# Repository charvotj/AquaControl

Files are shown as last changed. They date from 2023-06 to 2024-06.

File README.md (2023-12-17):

# Do not read me :)

It's work in progress and it's still completely uncomplete.

## Pro průběžný progress:
- [Verze odevzdaná jako semestrální](https://github.com/charvotj/AquaControl/tree/main/Semestr%C3%A1lka%20k%20odevzd%C3%A1n%C3%AD)
- [Poslední LaTeX build (text práce)](https://github.com/charvotj/AquaControl/blob/main/latex/CharvotBakalarka2023.pdf)
- [Schéma řídící jednotky (export do pdf)](https://github.com/charvotj/AquaControl/blob/main/latex/obrazky/exportovane/main-board-schematic.pdf)

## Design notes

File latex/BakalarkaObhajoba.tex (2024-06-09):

% Soubory musí být v kódování, které je nastaveno v příkazu \usepackage[...]{inputenc}

\documentclass[%        Základní nastavení
  %draft,    				  % Testovací překlad
  12pt,       				% Velikost základního písma je 12 bodů
	t,                  % obsah slajdů bude vždy začínat od shora (nebude vertikálně centrovaný)
	aspectratio=1610,   % poměr stran bude 16:10 (všechny projektory v učebnách na Technické 12 Brno),
	                    % další volby jsou 43, 149, 169, 54, 32.
	unicode,						% Záložky a informace budou v kódování unicode
]{beamer}				    	% Dokument třídy 'zpráva', vhodná pro sazbu závěrečných prací s kapitolami
%\usepackage{etex}

\usepackage[utf8]		  % Kódování zdrojových souborů je v UTF-8
	{inputenc}					% Balíček pro nastavení kódování zdrojových souborů
	
\usepackage{graphicx} % Balíček 'graphicx' pro vkládání obrázků
											% Nutné pro vložení logotypů školy a fakulty
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

\usepackage{cmap} 		% Balíček cmap zajišťuje, že PDF vytvořené `pdflatexem' je
											% plně "prohledávatelné" a "kopírovatelné"

%\usepackage{upgreek}	% Balíček pro sazbu stojatých řeckých písmem
											%% např. stojaté pí: \uppi
											%% např. stojaté mí: \upmu (použitelné třeba v mikrometrech)
											%% pozor, grafická nekompatibilita s fonty typu Computer Modern!

%\usepackage{amsmath} %balíček pro sabu náročnější matematiky

\usepackage{booktabs} % Balíček, který umožňuje v tabulce používat
                      % příkazy \toprule, \midrule, \bottomrule

%%%%%%%%%%%%%%%%%%%%%%%%%%%%%%%%%%%%%%%%%%%%%%%%%%%%%%%%%%%%%%%%%
%%%%%%      Definice informací o dokumentu             %%%%%%%%%%
%%%%%%%%%%%%%%%%%%%%%%%%%%%%%%%%%%%%%%%%%%%%%%%%%%%%%%%%%%%%%%%%%

\input{nastaveni}      % v tomto souboru doplňte údaje o sobě, o názvu práce...
                       % (tento soubor je sdílený s textem práce)

%%%%%%%%%%%%%%%%%%%%%%%%%%%%%%%%%%%%%%%%%%%%%%%%%%%%%%%%%%%%%%%%%%%%%%%%

%%%%%%%%%%%%%%%%%%%%%%%%%%%%%%%%%%%%%%%%%%%%%%%%%%%%%%%%%%%%%%%%%%%%%%%%
%%%%%%     Nastavení polí ve Vlastnostech dokumentu PDF      %%%%%%%%%%%
%%%%%%%%%%%%%%%%%%%%%%%%%%%%%%%%%%%%%%%%%%%%%%%%%%%%%%%%%%%%%%%%%%%%%%%%
%% Při vloženém balíčku 'hyperref' lze použít příkaz '\pdfsettings'
\pdfsettings
%  Nastavení polí je možné provést také ručně příkazem:
%\hypersetup{
%  pdftitle={Název studentské práce},    	% Pole 'Document Title'
%  pdfauthor={Autor studenstké práce},   	% Pole 'Author'
%  pdfsubject={Typ práce}, 						  	% Pole 'Subject'
%  pdfkeywords={Klíčová slova}           	% Pole 'Keywords'
%}
\hypersetup{pdfpagemode=FullScreen}       % otevření rovnou v režimu celé obrazovky
%%%%%%%%%%%%%%%%%%%%%%%%%%%%%%%%%%%%%%%%%%%%%%%%%%%%%%%%%%%%%%%%%%%%%%%

\usetheme{VUT} 				% barvy a rozložení prezentace odpovídající VUT FEKT
% alternativně lze použít jiná berevná témata, ale bez záruky. Například: 
%\usetheme{Darmstadt} \usecolortheme{default2}
\logoheader					% vytvoření zkráceného loga VUT FEKT v hlavičce slajdu, nechte odkomentované

					   %%%%%%%%%%%%%%%%%%%%%%%%%%%%%%%%%%%%%%%%%%%%%%%%%%%%%%%%%%%%%%%%%
%%%%%%      !!! VLASTNÍ BALÍČKY A NASTAVENÍ !!!        %%%%%%%%%%
%%%%%%%%%%%%%%%%%%%%%%%%%%%%%%%%%%%%%%%%%%%%%%%%%%%%%%%%%%%%%%%%%
%====== Units =====
% \usepackage{siunitx}
% \sisetup{inter-unit-product =\ensuremath{\cdot}}
% \sisetup{group-digits = integer}
% \sisetup{output-decimal-marker = {,}}
% \sisetup{exponent-product = \ensuremath{\cdot}}
% \sisetup{separate-uncertainty}
% \sisetup{tight-spacing = false}
% \DeclareSIUnit\permille{\text{\textperthousand}}
%\sisetup{scientific-notation = true}
%\sisetup{round-mode=places,round-precision=4}
%\sisetup{evaluate-expression}

%====== Hyperlinky ====== 
% \hypersetup{allbordercolors={1 1 1}}

%====== Obrazky ========
% \usepackage{graphicx} 
% \usepackage[dvipsnames]{xcolor} % E: option clash for package xcolor
% \usepackage{tikz}

% ^^ už tam někde prý jsou použité

\usepackage[siunitx]{circuitikz}
% \usepackage{pgf}
% \usetikzlibrary{matrix}
\usetikzlibrary{fit}
% \usetikzlibrary{patterns}
% \usepackage{tkz-euclide}
% \usetikzlibrary{arrows.meta, bending, patterns.meta, ducks}
% \usetikzlibrary{shapes, backgrounds, decorations.pathmorphing, calc}
\usetikzlibrary{positioning}

% % \usepackage{derivative} % nebude potřeba 

% \usepackage{pgfplots}
% \pgfplotsset{width=0.8\linewidth, compat=1.17}
% \def\plotcscale{0.8}
% \usepackage{pgfplotstable}
% \newcommand*\circled[1]{\tikz[baseline=(char.base)]{
%             \node[shape=circle,draw,inner sep=1pt] (char) {#1};}}

% \usepackage[style=iso-numeric,backend=biber]{biblatex}
% \addbibresource{text/literatura.bib}
%making everything to match Juice citations
% \DeclareFieldFormat{labelnumberwidth}{\mkbibbrackets{#1}}
% \usepackage{natbib}
% \usepackage{url}
% \DeclareUrlCommand\url{\def\UrlLeft{<}\def\UrlRight{>} \urlstyle{tt}}

% TEMP
\usepackage{multirow}
\usepackage{array}
\usepackage{tabularx}
\usepackage{calc}

\begin{document}

% v případě zakomentování následujícího se zobrazí v pravém dolním rohu slajdů klikatelné navigační symboly 
\disablenavigationsymbols

% titulní snímek, vysazen bez horních, dolních a postranních lišt (volba plain),
% není tak vysazen ani nadpis snímku
\maketitle

%%%%%%%%%%%%%%%%%%%%%%%%%%%%%%%%%%%%%%%%%%%%%%%%%%%%%%%%%%%%%%%%%%%%%%%
% 1. snímek s cíli (zadaním) práce
\begin{frame} 
	% nadpis snímku
	\frametitle{Cíle práce}
	Navrhnout zařízení pro automatické monitorování a řízení akvária:\\[0ex]
	%
	\begin{itemize}
		\item Průzkum trhu
		\item Stanovení požadavků
		\item Návrh zařízení
		\item Výroba
		\item Testování
	\end{itemize}
\end{frame}

% endregion

%%%%%%%%%%%%%
\begin{frame}[fragile]
	\frametitle{Průzkum trhu -- komerční řešení}
	
	\begin{columns}[T] 								% prostředí sloupce s umístěním nahoře
		\begin{column}{0.5\textwidth}		% první sloupec
			\begin{block}{Výhody}
				\begin{itemize}
					\item Všestrannost 
					\item Spolehlivost
				\end{itemize}
			\end{block}
			%
			\vspace{1.5ex}%
			\begin{alertblock}{Nevýhody}
				\begin{itemize}
					\item Vysoká cena 
					\item Převážně velmi komplexní
					\item Náročné nastavení systému
				\end{itemize}
			\end{alertblock}
			%
		\end{column}
		%
		\begin{column}{0.5\textwidth}		% druhý sloupec
			\begin{figure}%	
				\centering
				\vspace{-0.8cm}	              % horizontální mezera
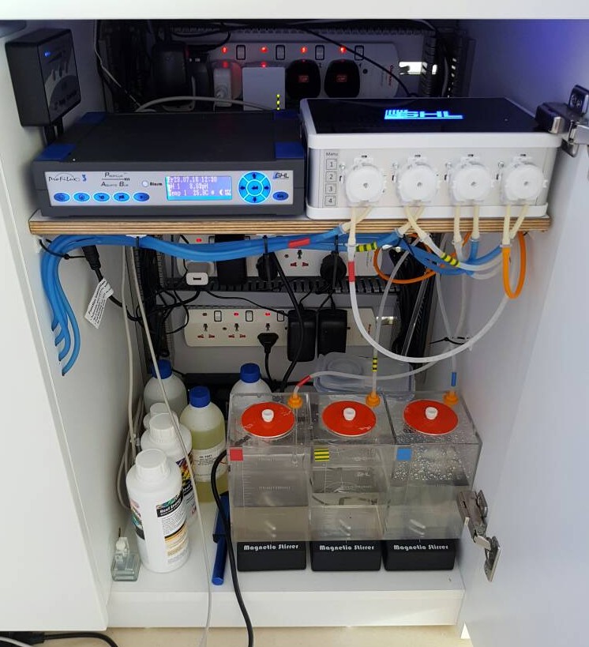
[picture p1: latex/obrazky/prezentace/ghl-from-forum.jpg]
				
				%lze vložit popisek, ale povetšinou je to v prezentaci zbytečné
				%\caption{Popisek obrázku}%
				%\label{obr:ukazka}
			\end{figure}
		\end{column}
	\end{columns}											% ukončení prostředí sloupce
\end{frame}

%%%%%%%%%%%%%
\begin{frame}[fragile]
	\frametitle{Průzkum trhu -- hobby řešení}
	
	\begin{columns}[T] 								% prostředí sloupce s umístěním nahoře
		\begin{column}{0.5\textwidth}		% první sloupec
			\begin{block}{Výhody}
				\begin{itemize}
					\item Návrh na míru 
					\item Nízká cena
				\end{itemize}
			\end{block}
			%
			\vspace{1.5ex}%
			\begin{alertblock}{Nevýhody}
				\begin{itemize}
					\item Návrh na míru
					\item Špatně rozšiřitelné
				\end{itemize}
			\end{alertblock}
			%
		\end{column}
		%
		\begin{column}{0.5\textwidth}		% druhý sloupec
			\begin{figure}%	
				\centering
				\vspace{-0.8cm}	              % horizontální mezera
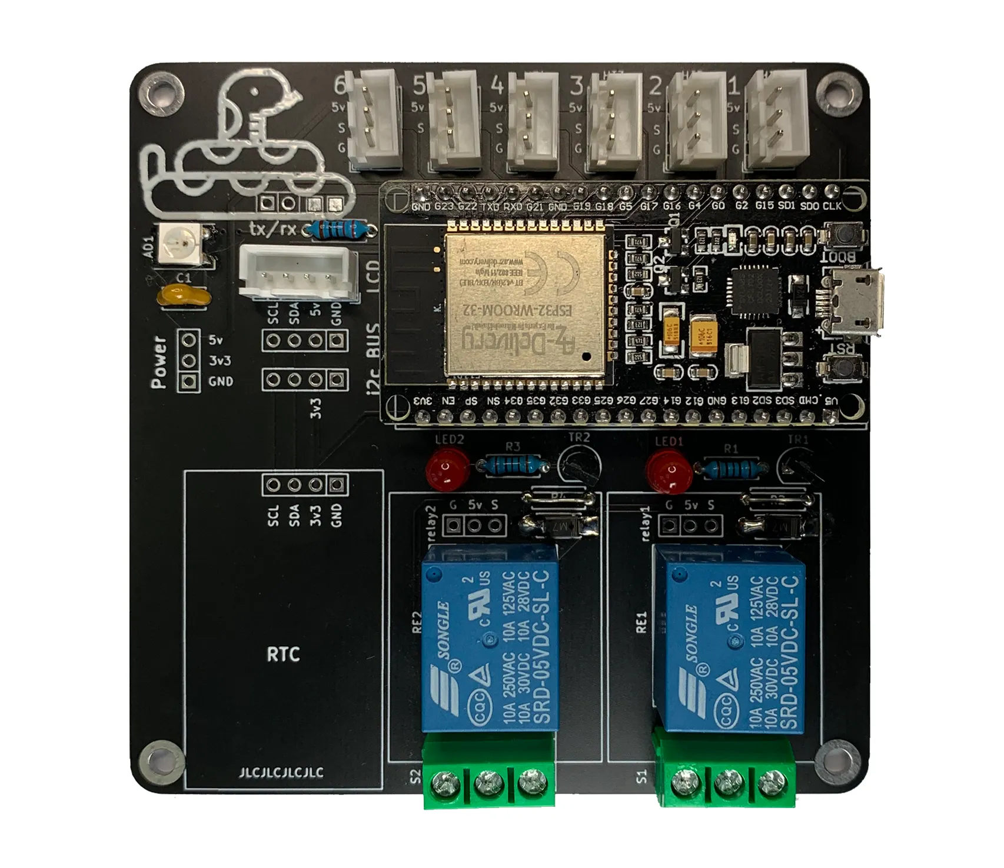
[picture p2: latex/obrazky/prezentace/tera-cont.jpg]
				
				%lze vložit popisek, ale povetšinou je to v prezentaci zbytečné
				%\caption{Popisek obrázku}%
				%\label{obr:ukazka}
			\end{figure}
		\end{column}
	\end{columns}											% ukončení prostředí sloupce
\end{frame}

%%%%%%%%%%%%%
\begin{frame}[fragile]
	\frametitle{Návrh vlastního zařízení -- Specifikace požadavků}
	
	\begin{columns}[T] 								% prostředí sloupce s umístěním nahoře
		\begin{column}{0.8\textwidth}		% první sloupec
			Určení zařízení:\\[1ex]
			%
			\begin{itemize}
				\item Malé sladkovodní akvária bez specifických potřeb
				\item Ovládání základních akčních členů a senzorů
			\end{itemize}
			\vspace{1.5ex}%
			Klíčové parametry:\\[1ex]
			\begin{itemize}
				\item Jednoduchost instalace a obsluhy
				\item Rozšiřitenost systému
				\item Nízká cena
			\end{itemize}
		\end{column}
		%
		\begin{column}{0.2\textwidth}		% druhý sloupec
			\begin{figure}%	
				\centering
				\vspace{2cm}	              % horizontální mezera
				\hspace{-4cm}
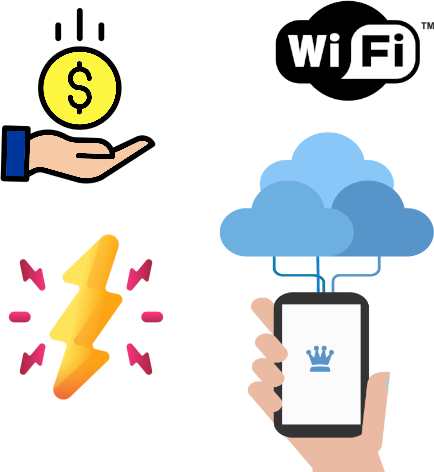
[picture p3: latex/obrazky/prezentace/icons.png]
				
				%lze vložit popisek, ale povetšinou je to v prezentaci zbytečné
				%\caption{Popisek obrázku}%
				%\label{obr:ukazka}
			\end{figure}
		\end{column}
	\end{columns}	% ukončení prostředí sloupce
\end{frame}

%%%%%%%%%%%%%
\begin{frame}[fragile]
	\frametitle{Blokové schéma -- Systém}
	\vspace{-0.8cm}
	\begin{figure}%	
		\centering
		\scalebox{0.6}
		{
		\begin{tikzpicture}[
			% scale=0.6, every node/.style={scale=0.6},
			shift={(30,30)},
			node distance=2cm,
			blok/.style={draw, rectangle, rounded corners=8pt, minimum height=1.5cm, minimum width=3cm},
			rect/.style={draw, dashed, blue, inner sep=15pt, fit={#1}},
			label/.style={blue}
		]
			% barvičky
			\definecolor{barva-silove}{RGB}{220, 220, 220}
			\definecolor{barva-ridici}{RGB}{241, 196, 15}
			% \draw (0,0) -- (4,0);
			\begin{scope}[]
				\node (napajeni) [blok, ] {Napájecí zdroj 24V};
				\node (ridici) [blok, below of = napajeni, align=center, fill=barva-ridici] {Řídicí jednotka \\ (ESP32)};
				\node (rele) [blok, right=0.5 of ridici, fill=barva-silove] {Relé modul};
				\node (zasuvky) [blok, right=0.5 of rele, fill=barva-silove] {Zásuvky 230VAC};
				\node (uzel) [style={draw, circle, minimum size=0.1cm, fill}, above=1cm of zasuvky] {};
				\node (sit) [blok, right=3 of uzel, fill=barva-silove ] {Přívod 230VAC};
				\node (display) [blok, below left=-0.5cm and 0.65cm of ridici] {Status displej};
				\node (ledstrip) [blok, above left=-0.5cm and 0.65cm of ridici] {Status LED pásek};
	
				\node (konektor1) [blok, align=center, below left=1.5cm and -1.2cm of ridici] {Konektor pro periferie \\ \#1};
				\node (konektor2) [blok, align=center, below right=1.5cm and -1.2cm of ridici] {Konektor pro periferie \\ \#2};
	
				% Periferie
				\node (per1-1) [blok, align=center, below=1.2cm of konektor1] {Periferie \\ \#1.1};
				\node (per1-x) [blok, align=center, below=1cm of per1-1] {Periferie \\ \#1.X};
			
				\node (per2-1) [blok, align=center, below=1.2cm of konektor2] {Periferie \\ \#2.1};
				\node (per2-y) [blok, align=center, below=1cm of per2-1] {Periferie \\ \#2.Y};
	
				% Popisek
				\node (vlastovka) [font=\fontsize{35}{14}\selectfont, yscale=3,  above right=-4.2cm and 0.6cm of per2-1] {\}}; 
	
				\node (popisek1) [font=\fontsize{18}{20}\selectfont,right=0.5cm of vlastovka,yshift=0cm, align=left] {Připojení senzorů: \\ -- teploměr \\ -- výška hladiny \\ -- pH \\ -- ...};
				\node (popisek2) [font=\fontsize{18}{20}\selectfont,right=1cm of popisek1.north east, anchor=north west, align=left] {Připojení akčních členů: \\ -- řízení LED svícení \\ -- automatické krmítko \\ -- ...};
				% \node (popisek3) [below=1cm of popisek2.south west, anchor=south west, align=left] {...};
	
				% Spojovací linie
				\draw[-] (sit) -- (uzel);
				\draw[-] (uzel) -- (napajeni);
				\draw[-] (uzel) -- (zasuvky);
				\draw[-] (napajeni) -- (ridici);
				\draw[-] (ridici) -- (napajeni);
				\draw[-] (ridici) -- (display);
				\draw[-] (ridici) -- (ledstrip);
				\draw[-] (ridici) -- (konektor1);
				\draw[-] (ridici) -- (konektor2);
				\draw[-] (ridici) -- (rele);
				\draw[-] (rele) -- (zasuvky);
		
				\draw[-] (konektor1) -- (per1-1);
				\draw[dashed] (per1-1) -- (per1-x);
				
				\draw[-] (konektor2) -- (per2-1);
				\draw[dashed] (per2-1) -- (per2-y);

				% Obdélník, který obklopí vybrané uzly
				\node (hlavni-cast) [rect={(napajeni) (display) (ledstrip) (konektor1) (zasuvky)}] {};
				\node[label,above left=0.2cm and -3.6cm of hlavni-cast] {Šasi řídicí jednotky};
			\end{scope}
		\end{tikzpicture}
		}
	\end{figure}
\end{frame}

%%%%%%%%%%%%%
\begin{frame}[fragile]
	\frametitle{Navržené zařízení -- prototyp}
	\vspace{-0.5cm}
	\begin{figure}%	
		% \hspace{-1.5cm}
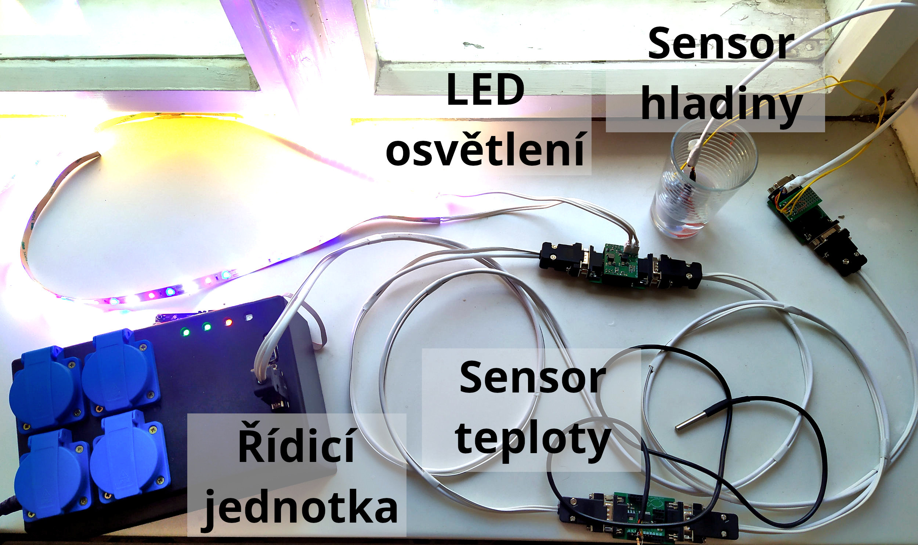
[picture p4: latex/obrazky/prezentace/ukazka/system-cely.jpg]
		
		%lze vložit popisek, ale povetšinou je to v prezentaci zbytečné
		%\caption{Popisek obrázku}%
		%\label{obr:ukazka}
	\end{figure}
\end{frame}

%%%%%%%%%%%%%
\begin{frame}[fragile]
	\frametitle{Návrh vlastního zařízení -- Řídicí jednotka}
	\vspace{-1cm}
	\begin{figure}%	
		% \hspace{-1.5cm}
		
		%lze vložit popisek, ale povetšinou je to v prezentaci zbytečné
		%\caption{Popisek obrázku}%
		%\label{obr:ukazka}
	\end{figure}
\end{frame}

%%%%%%%%%%%%%
\begin{frame}[fragile]
	\frametitle{Návrh vlastního zařízení -- Periferie}
		Periferie = samostatný blok připojený na sběrnici:\\[1ex]
		Univerzální modul:\\[1ex]
		%
		\begin{itemize}
			\item Vlastní MCU a regulátor napětí
			\item Komunikace po sběrnici 
			\item Napájení pro náročnější součásti (např. osvětlení)
		\end{itemize}
		\vspace{1ex}%
		%
		\begin{figure}%	
			% \hspace{-1.5cm}
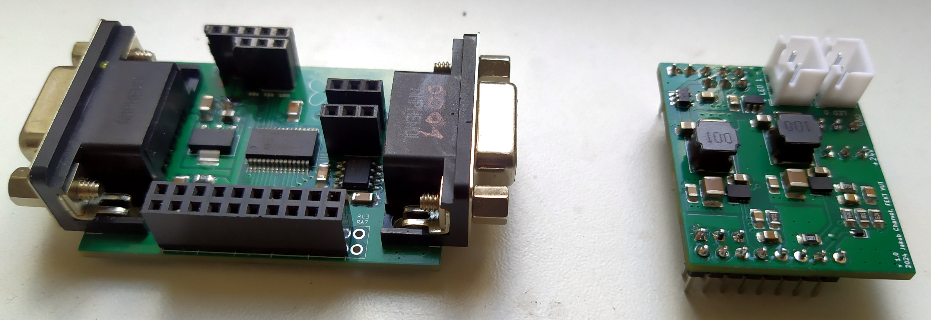
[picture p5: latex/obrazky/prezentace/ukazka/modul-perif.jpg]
			
			%lze vložit popisek, ale povetšinou je to v prezentaci zbytečné
			%\caption{Popisek obrázku}%
			%\label{obr:ukazka}
		\end{figure}

\end{frame}

%%%%%%%%%%%%%
\begin{frame}[fragile]
	\frametitle{Datová komunikace -- sběrnice  CAN}
	Tři typy zpráv:\\[1ex]
	\begin{itemize}
		\item To Slave -- požadavek řídicí jednotky
		\item To Master -- odpověď periferie
		\item Broadcast -- zpráva určená všem   
	\end{itemize}
	\vspace{2.5ex}%
	Průbeh komunikace:\\[1ex]
	\begin{itemize}
		\item Řídicí jednotka se pravidelně dotazuje periferií:
		\begin{itemize}
			\item Stav
			\item Data senzorů 
			\item Ovládání (akční členy)
		\end{itemize}
		\item Periferie pouze odpovídají na dotazy
	\end{itemize}
\end{frame}

%%%%%%%%%%%%%
\begin{frame}[fragile]
	\frametitle{Webové rozhraní}
	\vspace{-1cm}
	\begin{figure}%	
		% \hspace{-1.5cm}
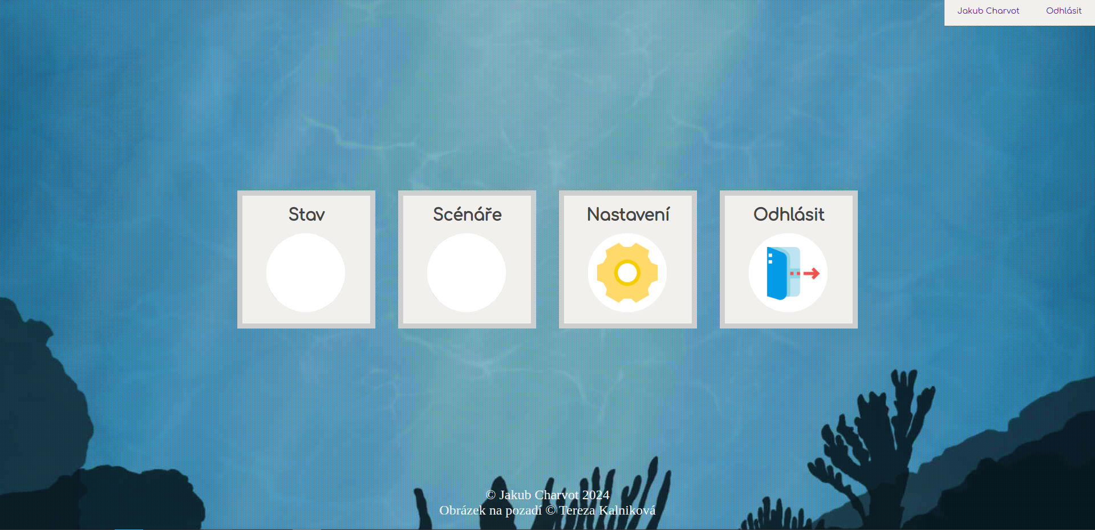
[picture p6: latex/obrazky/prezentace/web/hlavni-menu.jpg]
		
		%lze vložit popisek, ale povetšinou je to v prezentaci zbytečné
		%\caption{Popisek obrázku}%
		%\label{obr:ukazka}
	\end{figure}
\end{frame}

%%%%%%%%%%%%%
\begin{frame}[fragile]
	\frametitle{Webové rozhraní}
	\vspace{-1cm}
	\begin{figure}%	
		% \hspace{-1.5cm}
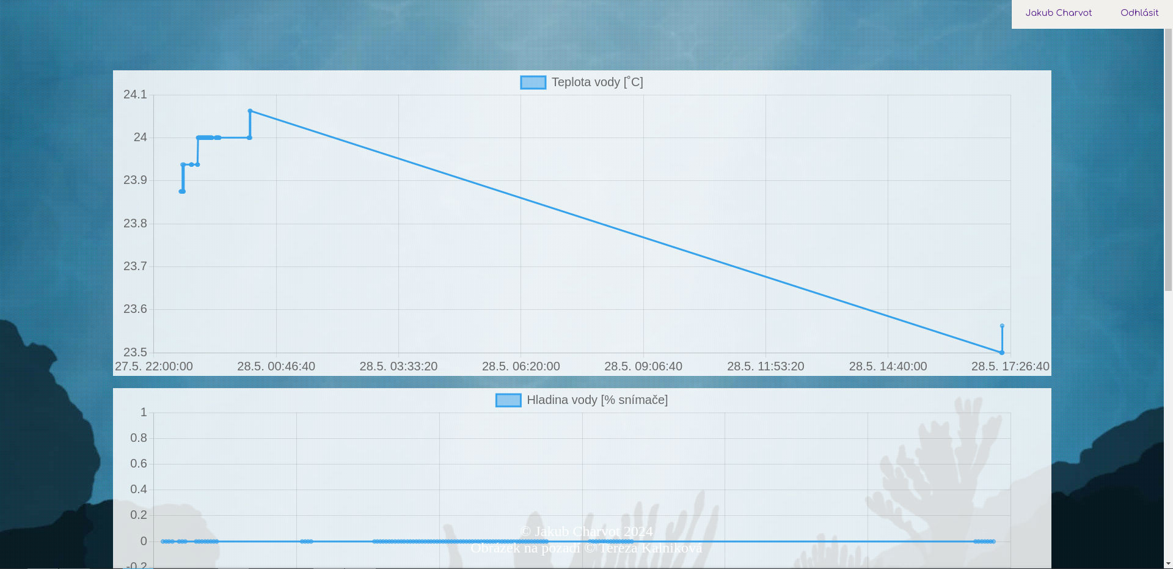
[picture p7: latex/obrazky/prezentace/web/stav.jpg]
		
		%lze vložit popisek, ale povetšinou je to v prezentaci zbytečné
		%\caption{Popisek obrázku}%
		%\label{obr:ukazka}
	\end{figure}
\end{frame}

%%%%%%%%%%%%%
\begin{frame}[fragile]
	\frametitle{Webové rozhraní}
	\vspace{-1cm}
	\begin{figure}%	
		% \hspace{-1.5cm}
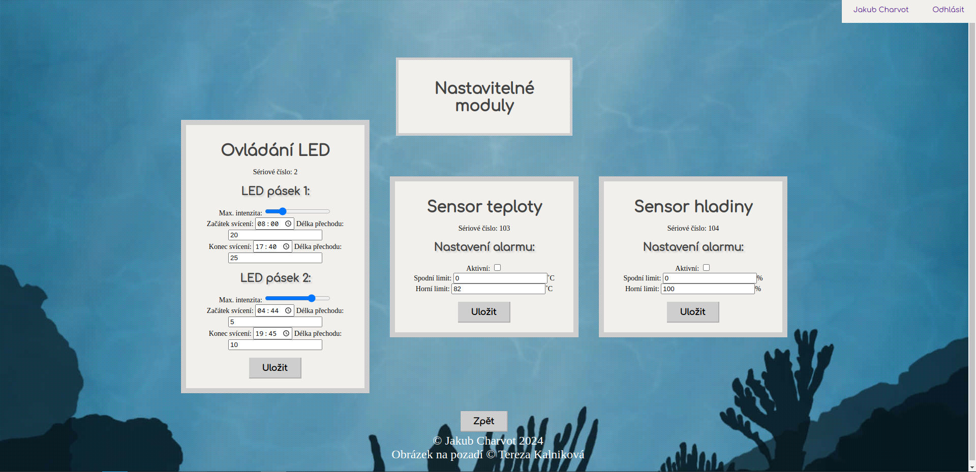
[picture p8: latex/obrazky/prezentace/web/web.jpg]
		
		%lze vložit popisek, ale povetšinou je to v prezentaci zbytečné
		%\caption{Popisek obrázku}%
		%\label{obr:ukazka}
	\end{figure}
\end{frame}

%%%%%%%%%%%%%
\begin{frame}[fragile]
	\frametitle{Budoucí plány a rozšíření}

	\begin{columns}[T] 								% prostředí sloupce s umístěním nahoře
		\begin{column}{0.5\textwidth}		% první sloupec
			\begin{block}{Blízká budoucnost}
				\begin{itemize}
					\item Oprava nalezených chyb
					\item Praktická aplikace v akváriu
					\item Přidání grafického displeje
					\item Výroba dalších periferií
				\end{itemize}
			\end{block}
		\end{column}
		%
		\begin{column}{0.5\textwidth}		% druhý sloupec
			\begin{alertblock}{Vzdálená budoucnost}
				\begin{itemize}
					\item Modifikace pro další oblasti domácí automatizace

				\end{itemize}
			\end{alertblock}
		\end{column}
	\end{columns}											% ukončení prostředí sloupce
\end{frame}

% podekovani
\begin{frame}[c] 
% bez nadpisu snímku
	\frametitle{\mbox{ }}
	\begin{center}
		{\Huge Děkuji za pozornost!}
	\end{center}
\end{frame}

% otázky oponenta
\begin{frame}[fragile] 
\frametitle{Otázky oponenta}
	\emph{Stanovte maximální provozní spotřebu všech periferií napájených LDO a stanovte jeho ztrátový výkon. Tyto údaje vám v bakalářské práci chybí.}\\[0.5ex]
	%
	\begin{figure}%	
		\centering
		\scalebox{0.9}
		{
			\begin{tikzpicture}[
				module/.style={%
			draw, rounded corners,
			minimum width=#1,
			minimum height=7mm,
			font=\sffamily,
			align=center
			},
		module/.default=2cm,
		>=LaTeX]
			
		% ridici
		\node[module] (24v) {Externí modul\\zdroje};
		\node[module, left=1.6cm of 24v] (sit) {Síť};
		\node[module, below=of 24v] (buck) {DC/DC měnič};
		\node[module, below=of buck] (ldo) {LDO}; 
		\node[module, below=of ldo] (mcu) {MCU};

		\node[module, right= of mcu] (konektor1) {Stavové LED};
		\node[module=1cm, right=of ldo] (konektor3) {Relé};

		\node[fit=(konektor1) (24v) (konektor3) (buck) (mcu), draw, inner sep=2mm] (fitridici) {};

		\node[module, right= 4cm of buck] (ldoperif) {LDO};
		\node[module, below=of ldoperif] (mcuperif) {MCU};
		\node[module, right= 4cm of 24v] (naro) {Náročné\\obvody};
		\node[module, right=of mcuperif] (nenaro) {Nenáročné\\obvody};

		\node[fit=(ldoperif) (mcuperif) (nenaro) (naro), draw, inner sep=2mm] (fitperif) {};

		% % Connections
		\draw[->] (sit)--(24v) node[midway, above] {\qty{230}{V}};		
		\draw[->] (24v)--(buck);
		\draw[->] (24v)--(naro) node[midway, above] {\qty{24}{V}};
		\draw[->] (buck)--(ldo);
		\draw[->] (buck)--(konektor1);
		\draw[->] (buck)--(konektor3);
		\draw[->] (ldo)--(mcu) node[midway, left] {\qty{3.3}{V}};
		\draw[->] (buck)--(ldoperif) node[midway, above] {\qty{5.2}{V}};
		\draw[->] (ldoperif)--(mcuperif) node[midway, left] {\qty{3.3}{V}};
		\draw[->] (ldoperif)--(nenaro);
			
		\end{tikzpicture}
		}
	\end{figure}
\end{frame}

% otázky oponenta
\begin{frame}[fragile] 
	\frametitle{Otázky oponenta}
	Řídicí jednotka:
	\begin{itemize}
		\item MCU: \(I_{TXpeak}= \qty{379}{mA}\), \(I_{TXavg}= \qty{239}{mA}\)
		\item CAN řadič: \(I_{IO_rdom}=\qty{500}{\micro A} \) 
	\end{itemize}
	\vspace{1cm}
	\begin{equation}
		I_{MAX} = \qty{379}{mA}+\qty{500}{\micro A} = \qty{379.5}{mA}
	\end{equation}
	\vspace{0.5cm}
		\begin{equation}
			P_{LDO} = (U_{IN} - U_{OUT})\cdot I_{MAX} = (\qty{5.2}{V} - \qty{3.3}{V})\cdot \qty{379.5}{mA} = \qty{721}{mW}
		\end{equation}
	\end{frame}

	% otázky oponenta
\begin{frame}[fragile] 
	\frametitle{Otázky oponenta}
	Periferie:
	\begin{itemize}
		\item MCU: \(I_{Vdd-max}= \qty{85}{mA}\)
		\item CAN řadič: \(I_{IO_rdom}=\qty{500}{\micro A} \) 
		\item Teplotní čidlo: \(I_{ds18b20} =\qty{1.5}{mA}\) 
	\end{itemize}
	\vspace{1cm}
	\begin{equation}
		I_{MAX} = \qty{85}{mA}+\qty{500}{\micro A}+\qty{1.5}{mA} = \qty{87}{mA}
	\end{equation}
	\vspace{0.5cm}
		\begin{equation}
			P_{LDO} = (U_{IN} - U_{OUT})\cdot I_{MAX} = (\qty{5.2}{V} - \qty{3.3}{V})\cdot \qty{87}{mA} = \qty{165}{mW}
		\end{equation}
	\end{frame}

% zdroje
\begin{frame} [fragile]
	% bez nadpisu snímku
	\frametitle{Zdroje obrázků}
	% \hspace{-5cm}
	\begin{itemize}
		\item \url{https://www.reef2reef.com/threads/lets-see-your-ghl.258905/#post-3069873}
		\item \url{https://brushknight.medium.com/terrarium-controller-idea-%EF%B8%8F-v1-4-b8ee96cfbd22}
		\item \url{https://www.pyramidions.com/blog/the-advantages-of-using-the-cloud-technology-for-app-development/}
		\item \url{https://www.flaticon.com/free-icons/money}
		\item \url{https://www.flaticon.com/free-icons/shock}
	\end{itemize}			
\end{frame}

%%%%%%%%%%%%%
\begin{frame}[fragile]
	\frametitle{Připojení periferií}
	
			Požadavky periferií:\\[1ex]
			%
			\begin{itemize}
				\item Napájení vlastního MCU
				\item Datová komunikace 
				\item Napájení výkonově náročnějších součástí (např. osvětlení)
			\end{itemize}
			\vspace{1.5ex}%
		%
		Konektor D-sub:\\[1ex]
		\begin{figure}[h!]
			\centering
			% trim=left bottom right top
			\begin{tikzpicture}
	
				% Draw the connector outline
				\draw[rounded corners=5pt] (0,0) -- (2,0) -- (2.6,1.5) -- (-0.6,1.5) -- cycle;
				
				% Draw the pins
				\newcounter{pinnum}
				\setcounter{pinnum}{9}
				\def\xoff{-0.25}
				\foreach \x in {0.5,1,...,2}
					\foreach \y in {0.6}
					{
						\draw (\xoff+\x,\y) circle (0.1);
						\node[anchor=north,font=\fontsize{9}{0}\selectfont] at (\xoff+\x,\y-0.03) {\thepinnum};
						\setcounter{pinnum}{\value{pinnum}-1}
					}
	
				\def\xoff{-0.5}
				\foreach \x in {0.5,1,...,2.5}
					\foreach \y in {1.0}
					{
						\draw (\xoff+\x,\y) circle (0.1);
						\node[anchor=south,font=\fontsize{9}{0}\selectfont] at (\xoff+\x,\y+0.03) {\thepinnum};
						\setcounter{pinnum}{\value{pinnum}-1}
					}
				
				% Pin numbers
				\node[anchor=west] (pin1) at (-4,1.4)                            {1,~5,~6,~9: GND};
				\node[below=0.6 of pin1.west,anchor=west] (pin2) {~~~~~~2,~7: \qty{24}{V}};
				\node[below=0.6 of pin2.west,anchor=west] (pin3) {~~~~~~~~~8: \qty{5.2}{V}};
				\node[anchor=west] at (2,1.1) (pin4) {~~~~~~~~~3: CAN High};
				\node[below=0.6 of pin4.west,anchor=west] (pin5) {~~~~~~~~~4: CAN Low};
				
			\end{tikzpicture}
		\end{figure}
\end{frame}

%%%%%%%%%%%%%
\begin{frame}[fragile]
	\frametitle{Blokové schéma -- Řídicí jednotka}
	\vspace{-0.7cm}
	\begin{figure}%	
		\centering
		\scalebox{0.9}
		{
			\begin{tikzpicture}[
				module/.style={%
			draw, rounded corners,
			minimum width=#1,
			minimum height=7mm,
			font=\sffamily,
			align=center
			},
		module/.default=2cm,
		>=LaTeX]
			
				% ridici
				\node[module] (mcu) {MCU};
				\node[module, left=of mcu] (ldo) {LDO}; 
				\node[module, above=of ldo] (buck) {DC/DC měnič};
				\node[module, right=of mcu] (candriver) {CAN řadič};
				\node[module, above right=10mm and -5mm of candriver] (konperif) {Konektory periferií};
				\node[module, above=of buck] (24v) {Externí modul\\Zdroj \qty{24}{V}};
				\node[module, below=of mcu] (konektory) {Konektory};
				\node[module=1cm, below right=9mm and -7mm of konektory] (konektor1) {Stavové LED};
				\node[module=1cm, below left= 9mm and -8mm of konektory] (konektor2) {Displej};
				\node[module=1cm, below right= 0mm and 6mm of konektory] (konektor3) {Relé};
				\node[module=1cm, below left= 0mm and 6mm of konektory] (konektor4) {Rozšíření};
	
				\node[fit=(konektor1) (konektor2) (konektor3) (konektor4) (buck) (konperif) (mcu), draw, inner sep=2mm] (fitridici) {};
				% Connections
				\foreach \i in {1,2,3}
					\draw[->] (konektory)--(konektor\i);
				\draw[<->] (konektory)--(konektor4);
				\draw[<->] (konektory)--(mcu);
				\draw[->] (buck)--(ldo);
				\draw[->] (ldo)--(mcu);
				\draw[<->] (candriver)--(mcu);
				\draw[->] (buck)--(konperif);
				\draw[<->] (candriver)--(konperif);
	
				\draw[->,dashed] (24v) to [out=0,in=115] (konperif);
				\draw[->,dashed] (24v)--(buck);
			
			\end{tikzpicture}
		}
	\end{figure}
\end{frame}

%%%%%%%%%%%%%
\begin{frame}[fragile]
	\frametitle{Blokové schéma -- Software}
	\vspace{-0.65cm}
	\begin{figure}%	
		\centering
		\scalebox{0.7}
		{
			\begin{tikzpicture}[
				module/.style={%
			draw, rounded corners,
			minimum width=#1,
			minimum height=7mm,
			font=\sffamily,
			align=center
			},
		module/.default=2cm,
		>=LaTeX]
			
				% ridici
				\node[module] (freertos) {Free RTOS};
				\node[module, below=of freertos] (tasks) {Tasks};
				\node[module=1cm, below right=9mm and -7mm of tasks] (task1) {Relé};
				\node[module=1cm, below left= 9mm and -8mm of tasks] (task2) {WiFi};
				\node[module=1cm, below right= 3mm and 4mm of tasks] (task3) {CAN};
				\node[module=1cm, below left= 3mm and 4mm of tasks] (task4) {Status};
	
				\node[fit=(task1) (task2) (task3) (task4) (freertos), draw, inner sep=2mm,label={[yshift=2mm, font=\sffamily]Řídicí jednotka}] (fitridici) {};
				% Connections
				\foreach \i in {1,2,3,4}
					\draw[->] (tasks)--(task\i);
				\draw[<->] (tasks)--(freertos);
	
				% WS
				\node[module, below=1.5cm of {task4.west|-fitridici.south}, anchor=north west] (api) {API};
				\node[module, below=of api] (php) {PHP};
				\node[module, below=of php] (mysql) {mySQL DB};
				\node[module, right= of php] (userweb) {Uživatelský \\panel};
				\node[fit={(php) (userweb) (api) (mysql) (mysql-|fitridici.west) (mysql-|fitridici.east) }, draw, inner xsep=\pgflinewidth, inner ysep=2mm, label={[yshift=2mm, font=\sffamily]Web server}] (fitWS) {};
				\draw[<->] (api)--(php);
				\draw[<->] (php)--(mysql);
				\draw[<->] (php)--(userweb);
			
				% perif
				\node[module, right=1.5cm of {task3-|fitridici.east}] (isr) {ISR};
				\node[module, right=3mm of isr.north east, anchor=north west] (can) {Obsluha\\CAN příkazů};
				\node[module, above= 7mm of can.north east, anchor=south east] 
					(programloop) {Smyčka programu};
				\node[module, above=5mm of programloop] (dataprocess) {Zpracování dat};
				
				\node[fit={(can) (isr) (dataprocess|-fitridici.south) (dataprocess|-fitridici.north)}, draw, inner xsep=2mm, inner ysep=\pgflinewidth, label={[yshift=2mm, font=\sffamily]Periferie}] (fitperif) {};
				\node[module, right=1.5cm of dataprocess] (sensory) {Sensory};
				\draw[->] (isr)--(can);
				\draw[<->] (programloop)--(dataprocess);
				
				%arrow between boxes
				\draw[<->,dashed] (task2) to [out=-135,in=90] (api);
				\draw[->,dashed] (task3)--(isr);
				\draw[->,dashed] (can) to [out=-150,in=-45] (task3);
				\draw[<-,dashed] (dataprocess) -- (sensory);
			\end{tikzpicture}
		}
	\end{figure}
\end{frame}

%%%%%%%%%%%%%
\begin{frame}[fragile]
	\frametitle{Stavové LED řídicí jednotky}
	\vspace{-0.65cm}
	\begin{figure}%	
		\centering
		\scalebox{0.8}
		{
			\begin{tikzpicture}
                % Draw a rectangle
                \draw[thick] (0,0) rectangle (3*4,1);
                
                % Draw and fill four colorful circles
                \filldraw[fill=green,draw=black,thin]  (3*0.5, 0.5) circle (0.3) node[align=center,above=0.5] {\textbf{Stav zařízení}};
                \filldraw[fill=green,draw=black,thin]  (3*1.5, 0.5) circle (0.3) node[align=center,above=0.5] {\textbf{Stav WiFi}};
                \filldraw[fill=black,draw=black,thin]  (3*2.5, 0.5) circle (0.3) node[align=center,above=0.5] {\textbf{Alarm 1}};
                \filldraw[fill=black,draw=black,thin]  (3*3.5, 0.5) circle (0.3) node[align=center,above=0.5] {\textbf{Alarm 2}};

                % Draw and fill four colorful circles
                \filldraw[fill=blue,draw=black,thin]    (3*0.5, -1.5*0.8) circle (0.3) node[align=center,above=0.35] {Nedefinováno};
                \filldraw[fill=blue,draw=black,thin]    (3*1.5, -1.5*0.8) circle (0.3) node[align=center,above=0.35] {Nedefinováno};
                \filldraw[fill=blue,draw=black,thin]    (3*2.5, -1.5*0.8) circle (0.3) node[align=center,above=0.35] {Nedefinováno};
                \filldraw[fill=blue,draw=black,thin]  (3*3.5, -1.5*0.8) circle (0.3) node[align=center,above=0.35] {Nedefinováno};

                % Draw and fill four colorful circles
                \filldraw[fill=magenta,draw=black,thin] (3*0.5, -3.5*0.8) circle (0.3) node[align=center,above=0.35] {Inicializace};
                \filldraw[fill=magenta,draw=black,thin] (3*1.5, -3.5*0.8) circle (0.3) node[align=center,above=0.35] {Inicializace};
                \filldraw[fill=orange,draw=black,thin]  (3*2.5, -3.5*0.8) circle (0.3) node[align=center,above=0.35] {Upozornění};
                \filldraw[fill=orange,draw=black,thin]  (3*3.5, -3.5*0.8) circle (0.3) node[align=center,above=0.35] {Upozornění};

                % Draw and fill four colorful circles
                \filldraw[fill=green,draw=black,thin]   (3*0.5, -5.5*0.8) circle (0.3) node[align=center,above=0.35] {Ok};
                \filldraw[fill=orange,draw=black,thin]  (3*1.5, -5.5*0.8) circle (0.3) node[align=center,above=0.35] {Připojeno};
                \filldraw[fill=red,draw=black,thin]   (3*2.5, -5.5*0.8) circle (0.3) node[align=center,above=0.35] {Alarm};
                \filldraw[fill=red,draw=black,thin]  (3*3.5, -5.5*0.8) circle (0.3) node[align=center,above=0.35] {Alarm};

                % Draw and fill four colorful circles
                \filldraw[fill=red,draw=black,thin]     (3*0.5, -7.5*0.8) circle (0.3) node[align=center,above=0.35] {Chyba};
                \filldraw[fill=green,draw=black,thin]   (3*1.5, -7.5*0.8) circle (0.3) node[align=center,above=0.35] {Online};
                \filldraw[fill=black,draw=black,thin]   (3*2.5, -7.5*0.8) circle (0.3) node[align=center,above=0.35] {OK};
                \filldraw[fill=black,draw=black,thin]   (3*3.5, -7.5*0.8) circle (0.3) node[align=center,above=0.35] {OK};

                % Draw and fill four colorful circles
                \filldraw[fill=red,draw=black,thin]     (3*1.5, -9.5*0.8) circle (0.3) node[align=center,above=0.35] {Chyba};
            \end{tikzpicture}
		}
	\end{figure}
\end{frame}

%%%%%%%%%%%%%
\begin{frame} 
	\frametitle{Vybavení akvária}
	
	\begin{columns}[T] 								% prostředí sloupce s umístěním nahoře
		\begin{column}{0.4\textwidth}		% první sloupec
			Požadavky jsou určeny:\\[0ex]
			%
			\begin{itemize}
				\item Velikostí nádrže
				\item Výběrem osazenstva 
				\item Slaná / sladká voda 
			\end{itemize}

			\vspace{2ex}%
			Základní technika:\\[0ex]
			%
			\begin{itemize}
				\item Filtr vody
				\item Topné těleso
				\item Osvětlení 
				\item Senzory
			\end{itemize}
		\end{column}
		%
		\begin{column}{0.6\textwidth}		% druhý sloupec
			\begin{figure}%	
				\centering
				% \vspace{1cm}	              % horizontální mezera
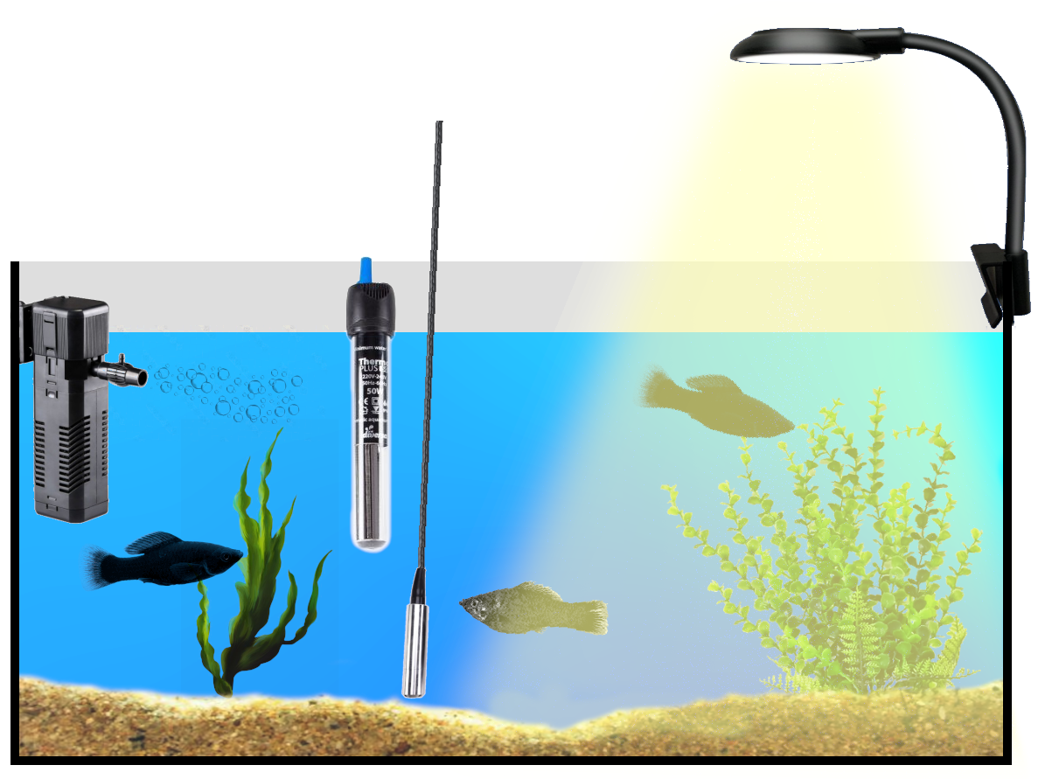
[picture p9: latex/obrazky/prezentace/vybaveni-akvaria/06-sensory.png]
				
				%lze vložit popisek, ale povetšinou je to v prezentaci zbytečné
				%\caption{Popisek obrázku}%
				%\label{obr:ukazka}
			\end{figure}
		\end{column}
	\end{columns}											% ukončení prostředí sloupce
\end{frame}

\end{document}

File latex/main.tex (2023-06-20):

% !TeX encoding = UTF-8

\documentclass{customarticle}

\graphicspath{ {./img/} }
% \addbibresource{bibliography.bib} % + odkomentovat i v .cls souuboru

\author{Jakub Charvot}
\title{Bakalářská práce -- poznámky}

% =========================================
% =============== DOKUMENT ================
% =========================================
\begin{document}
	%====== Vygenerování tabulky ======
	\maketitle

\section*{Cíl}
	Vytvořit zařízení pro kontrolu a ovládání domácího akvária. Jedná se o kompletní přepracování a rozšíření mého staršího projektu z doby gymnaziální.
	
	Požadovaná funkčnost:
	\begin{itemize}
		\item Ovládání světel
		\item Kontrola teploty a výšky hladiny
		\item Vzdálený přístup k systému přes webové rozhraní
		\item Vše na jedné DPS + konektory pro senzory a napájení
	\end{itemize}

	Rád bych přidal, ale ještě musím promyslet:
	\begin{itemize}
		\item Ovládání filtru vody (zapnutí/vypnutí)
		\item Automatické krmítko
		\item Případně další senzory, kamera
	\end{itemize}

	Chci se snažit zařízení připravit co nejvíce tak, aby bylo možné ho začít prodávat (to není mým cílem, ale přijde mi, že se tam naučím dělat věci správně), tedy aby byla práce s ním intuitivní a nebylo potřeba diplomu jen k tomu, aby ho uživatel zapnul a nastavil.

\clearpage
\section*{Popis akvária pro představu}
	Jedná se o malé domácí akvárium o objemu přibližně \qty{30}{\litre}. Pro správnou funkci je potřeba regulovat teplotu vody, filtrovat a doplňovat vodu, také je potřeba svítit a to nejlépe s plynulým rozsvěcováním a zhasínáním. Rybky krmíme 1 až 2 krát denně ručně, v případě dovolené instalujeme automatické krmítko na tužkové baterie.
	\begin{figure}[!h]
		\centering
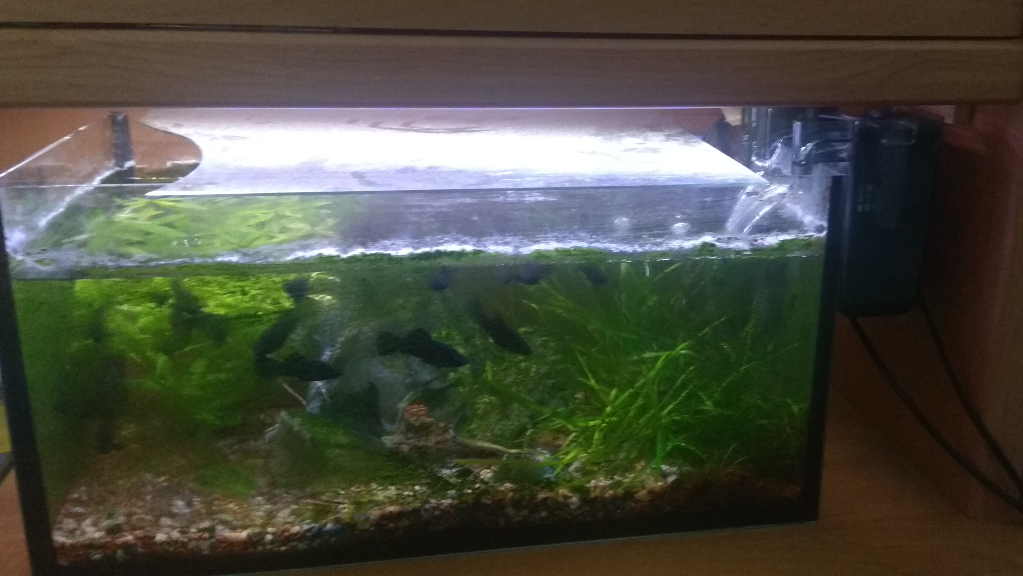
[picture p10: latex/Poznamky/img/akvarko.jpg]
		
		\caption{Naše akvárium, souhrnné foto.}
		\label{fig:akvarko}
	\end{figure}

	\begin{figure}[!h]
		\centering
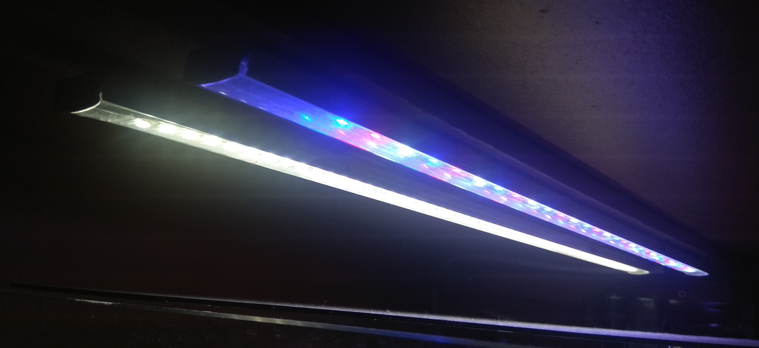
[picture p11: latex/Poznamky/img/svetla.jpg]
		
		\caption{Osvětlení formou dvou běžných LED pásků, ovládám každý zvlášť.}
		\label{fig:svetla}
	\end{figure}
	
	\begin{figure}[!h]
		\centering
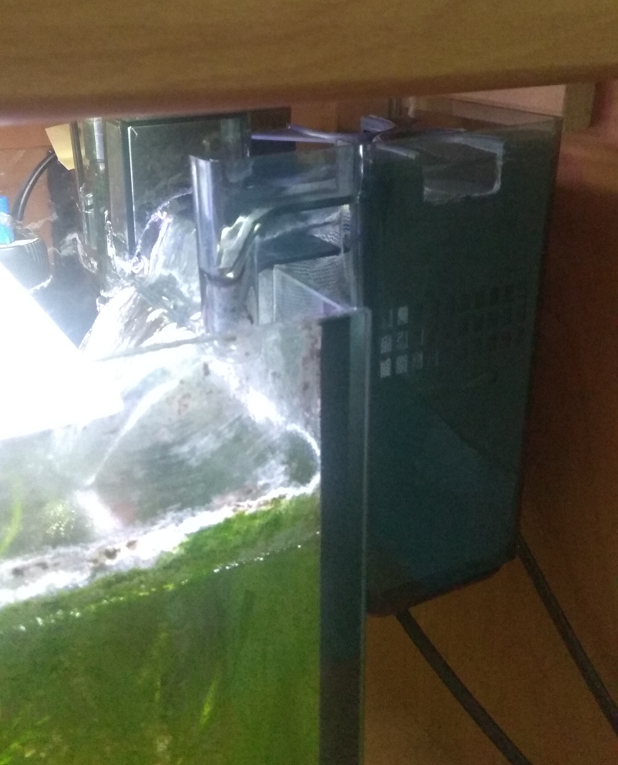
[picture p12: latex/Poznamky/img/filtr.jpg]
		
		\caption{Detail filtru.}
		\label{fig:filtr}
	\end{figure}

	\begin{figure}[!h]
		\centering
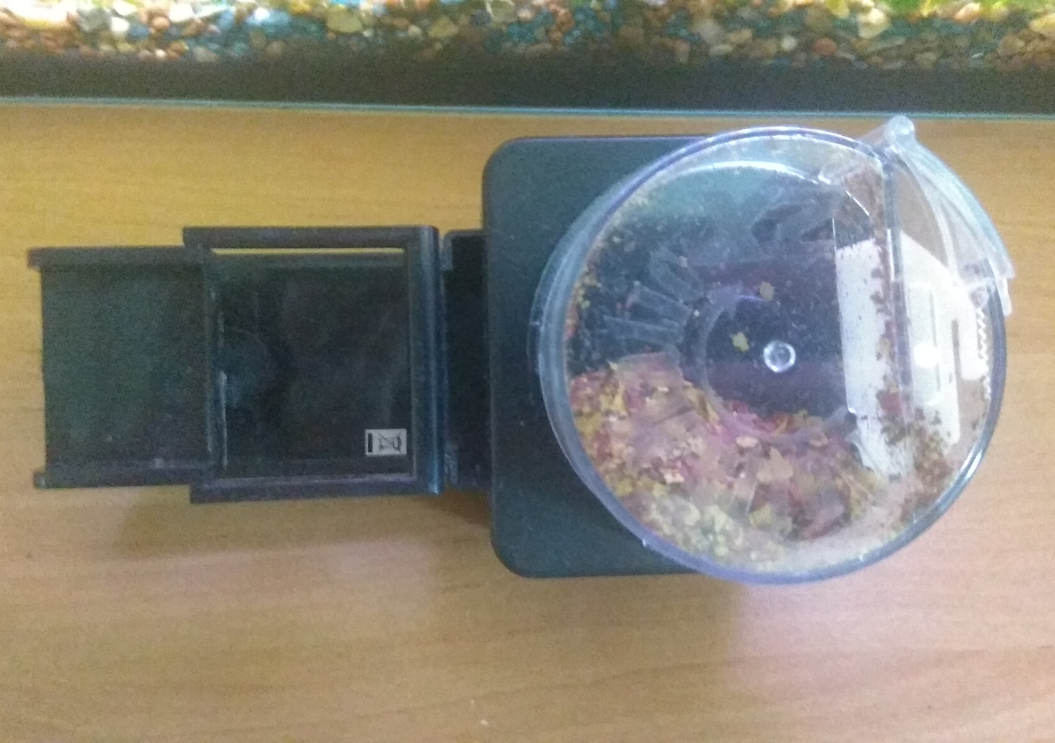
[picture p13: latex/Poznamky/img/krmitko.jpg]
		
		\caption{Automatické krmítko na baterie, rád bych nahradil vlastním řešením.}
		\label{fig:krmitko}
	\end{figure}

\clearpage
\section*{Popis verze Alpha :)}
	\begin{figure}[!h]
		\centering
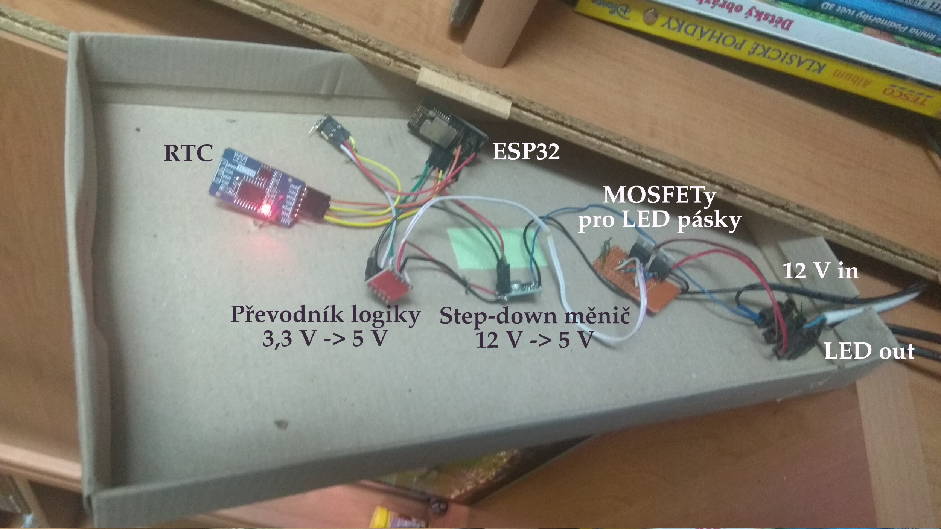
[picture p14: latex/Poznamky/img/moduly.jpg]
		
		\caption{moduly}
		\label{fig:moduly}
	\end{figure}
	Starší středoškolský projekt je vytvořený na úrovni modulů, je použit kontroler ESP32, na kterém běží webserver. Zařízení slouží pouze k ovládání světel, přes webovou stránku lze nastavit čas a rychlost rozsvícení a zhasnutí. 
	
	Kód je psán v Arduino frameworku, což byla v danou chvíli rozumná volba, ale teď bych se mu rád pokusil vyhnout. 
	Pro ovládání světel (LED pásky) jsem použil mosfet tranzistory řízené PWM pinem, také nebyly zvoleny vhodně, musel jsem použít předovník úrovně z \qty{3.3}{\volt} na \qty{5}{\volt}, aby bylo možné tranzistor plně otevřít.

	Za běžných podmínek zařízení funguje, ale například po výpadku elektřiny často končí v bootovací smyčce a je potřeba ručně zmáčknout reset, na stabilitu bych se tedy taky rád zaměřil.

\end{document}

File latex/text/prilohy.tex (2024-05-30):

\chapter{Schéma a návrh \acs{dps} řídicí jednotky}
	\label{priloha:schema-a-dps-ridici-jednotka}
	\section{Blokové schéma}
	\label{priloha:schema-ridici-jednotka-blokove}
		% trim=left bottom right top
		\includegraphics
		[
			width=\textheight, height=0.9\textwidth, keepaspectratio,
			page=1, 
			angle=90,
			trim=1.5cm 1cm 0cm 1cm, 
			clip
		]{obrazky/exportovane/main-board-schematic.pdf}

	\section{Zapojení \acs{mcu}}
	\label{priloha:schema-ridici-jednotka-mcu}
		% trim=left bottom right top
		\includegraphics
		[
			width=\textheight, height=\textwidth, keepaspectratio,
			page=2, 
			angle=90,
			trim=1.5cm 1cm 0cm 1cm, 
			clip
		]{obrazky/exportovane/main-board-schematic.pdf}

	\section{Napájecí obvod}
	\label{priloha:schema-ridici-jednotka-napajeci-obvod}
		% trim=left bottom right top
		\includegraphics
		[
			width=\textheight, height=\textwidth, keepaspectratio,
			page=3, 
			angle=90,
			trim=1.5cm 1cm 0cm 1cm, 
			clip
		]{obrazky/exportovane/main-board-schematic.pdf}

	\section{Konektory}
	\label{priloha:schema-ridici-jednotka-konektory}
		% trim=left bottom right top
		\includegraphics
		[
			width=\textheight, height=\textwidth, keepaspectratio,
			page=4, 
			angle=90,
			trim=1.5cm 1cm 0cm 1cm, 
			clip
		]{obrazky/exportovane/main-board-schematic.pdf}

	\section{Sběrnice periferií}
	\label{priloha:schema-ridici-jednotka-periferie}
		% trim=left bottom right top
		\includegraphics
		[
			width=\textheight, height=\textwidth, keepaspectratio,
			page=5, 
			angle=90,
			trim=1.5cm 1cm 0cm 1cm, 
			clip
		]{obrazky/exportovane/main-board-schematic.pdf}
	
	\section{Vodivé motivy \acs{dps}}
	\label{priloha:dps-main-board}
		\begin{tikzpicture}
			% Define the width of each image
			\newcommand{\imagewidth}{0.45\linewidth}
			\newcommand{\rowheight}{0.75\linewidth}
			\newcommand{\pdffilepath}{obrazky/exportovane/mainBoardDPS/color.pdf}
			% \newcommand{\pdffilepath}{obrazky/exportovane/mainBoardDPS/bw.pdf} %BW version
		
			% Row 1
			\node[anchor=south west,inner sep=0, label={[align=center]Vodivý motiv horní strany \\(F.Cu)}] at (0, 0) {};
			\node[anchor=south west,inner sep=0, label={[align=center]Vodivý motiv spodní strany\\(B.Cu)}] at (\imagewidth, 0) {};
		
			% Row 2
			\node[anchor=south west,inner sep=0, label={[align=center]Vodivý motiv 1. vnitřní vrstvy\\(In1.Cu)}] at (0, -\rowheight) {};
			\node[anchor=south west,inner sep=0, label={[align=center]Vodivý motiv 2. vnitřní vrstvy\\(In2.Cu)}] at (\imagewidth, -\rowheight) {};
		\end{tikzpicture}

\chapter{Schéma a návrh \acs{dps} modulu periferií}
\label{priloha:schema-a-dps-modul-periferii}
\section{Vodivé motivy \acs{dps}}
\label{priloha:dps-modul-periferii}
	\begin{tikzpicture}
		% Define the width of each image
		\newcommand{\imagewidth}{0.48\linewidth}
		\newcommand{\rowheight}{0.65\linewidth}
		\newcommand{\pdffilepath}{obrazky/exportovane/peripherialModuleDPS/color.pdf}
		% \newcommand{\pdffilepath}{obrazky/exportovane/mainBoardDPS/bw.pdf} %BW version

		% Row 1
		\node[anchor=south west,inner sep=0, label={[align=center]Vodivý motiv horní strany \\(F.Cu)}] at (0, 0) {};
		\node[anchor=south west,inner sep=0, label={[align=center]Vodivý motiv spodní strany\\(B.Cu)}] at (\imagewidth, 0) {};

		% Row 2
		\node[anchor=south west,inner sep=0, label={[align=center]Vodivý motiv 1. vnitřní vrstvy\\(In1.Cu)}] at (0, -\rowheight) {};
		\node[anchor=south west,inner sep=0, label={[align=center]Vodivý motiv 2. vnitřní vrstvy\\(In2.Cu)}] at (\imagewidth, -\rowheight) {};
	\end{tikzpicture}

	\section{Schéma zapojení}
	\label{priloha:schema-modul-periferii}
		% trim=left bottom right top
		\includegraphics
		[
			width=\textheight, height=\textwidth, keepaspectratio,
			page=1, 
			angle=90,
			trim=1.5cm 1cm 0cm 1cm, 
			clip
		]{obrazky/exportovane/peripherial-module-schematic.pdf}

\chapter{Schéma a návrh \acs{dps} modulu \acs{led} osvětlení}
\label{priloha:schema-a-dps-led-board}

\section{Vodivé motivy \acs{dps}}
\label{priloha:dps-led-board}
\begin{tikzpicture}
	% Define the width of each image
	\newcommand{\imagewidth}{0.48\linewidth}
	\newcommand{\rowheight}{0.5\linewidth}
	\newcommand{\pdffilepath}{obrazky/exportovane/ledBoardDPS/color.pdf}
	% \newcommand{\pdffilepath}{obrazky/exportovane/mainBoardDPS/bw.pdf} %BW version
	
	% Row 1
	\node[anchor=south west,inner sep=0, label={[align=center]Vodivý motiv horní strany \\(F.Cu)}] at (0, 0) {};
	\node[anchor=south west,inner sep=0, label={[align=center]Vodivý motiv spodní strany\\(B.Cu)}] at (\imagewidth, 0) {};
	
	% Row 2
	\node[anchor=south west,inner sep=0, label={[align=center]Vodivý motiv 1. vnitřní vrstvy\\(In1.Cu)}] at (0, -\rowheight) {};
	\node[anchor=south west,inner sep=0, label={[align=center]Vodivý motiv 2. vnitřní vrstvy\\(In2.Cu)}] at (\imagewidth, -\rowheight) {};
\end{tikzpicture}

\section{Schéma zapojení}
\label{priloha:schema-led-board}
% trim=left bottom right top
\includegraphics
[
	width=\textheight, height=\textwidth, keepaspectratio,
			page=1, 
			angle=90,
			trim=1.5cm 1cm 0cm 1cm, 
			clip
		]{obrazky/exportovane/led-board-schematic.pdf}

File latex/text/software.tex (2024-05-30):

\chapter{Software}
    Tato kapitola se věnuje popisu návrhu softwaru pro jednotlivé části systému řízení akvária. Jak již bylo zmíněno v~předchozích kapitolách, systém se skládá z~řídicí jednotky, ke které jsou připojeny jednotlivé periferie a která komunikuje s~webovým serverem za pomoci WiFi. Každá ze zmíněných částí pak potřebuje vlastní zdrojový kód. 
    
    K~programování a testování byla použita dvě vývojová prostředí. Visual Studio Code je open source řešení spravované společností Microsoft a díky široké škále doplňků umožňuje velmi univerzální použití. S~přidaným rozšířením ESP-IDF je také preferovaným prostředím společnosti Espressif, bylo tedy využito pro tvorbu kódu řidicí jednotky, stejně tak i pro webové rozhraní. Pro programování periferií bylo zvoleno prostředí MPLAB X. Jedná se o~řešení společnosti Microchip určené speciálně pro programování mikrokontrolérů této firmy. Součástí je kromě samotného editoru také kompilátor, možnost debugování kódu nebo modul zvaný Code Configurator sloužící pro generování jednoduchého HAL (Hardware Abstraction Level) kódu.

    V~této chvíli software odpovídá podobě zbytku zařízení -- tedy jedná se o~prototyp určený primárně k~demonstraci funkce zařízení. Aby byl kód použitelný v~reálné aplikaci a choval se zde spolehlivě, je potřeba podrobit jej rozsáhlejšímu testování a také lépe ošetřit chování zařízení v~různých nežádoucích stavech.   

% \clearpage
\section{Architektura}
    Na obr.~\ref{fig:sw-blokove-schema} se nachází blokové schéma systému z~pohledu softwaru. Obrázek slouží primárně pro lepší orientaci čtenáře v~této kapitole, obsahuje pouze klíčové části a některé věci zjednodušuje. Podrobněji se jednotlivým blokům věnují další podkapitoly. Obdélník popsaný v~obrázku jako \uv{Periferie} popisuje strukturu kódu platnou pro všechny periferie, je ale samozřejmé, že periferií této struktury bude v~systému připojeno vícero.

    Propojení přerušovanými šipkami v~obrázku značí komunikaci mezi dvěma částmi s~odlišným programem. Z~hlediska internetové komunikace se navržené zařízení chová jako klient, tedy neposlouchá na žádném portu a z~vnější sítě není nijak dostupné. Webový server disponuje datovým rozhraním (API), kterého se zařízení v~pravidelných intervalech dotazuje na případné změny konfigurace a prostřednictvím kterého zasílá na server data ze svého běhu. Při komunikaci mezi řídicí jednotkou a periferiemi pak řídicí jednotka funguje jako \uv{master} a periferie odpovídají pouze v~reakci na dotaz z~její strany.

    % Blokove schema
    \begin{figure}[h!]
        \centering
        \begin{tikzpicture}[
            module/.style={%
        draw, rounded corners,
        minimum width=#1,
        minimum height=7mm,
        font=\sffamily,
        align=center
        },
    module/.default=2cm,
    >=LaTeX]
        
            % ridici
            \node[module] (freertos) {Free RTOS};
            \node[module, below=of freertos] (tasks) {Tasks};
            \node[module=1cm, below right=9mm and -7mm of tasks] (task1) {Relé};
            \node[module=1cm, below left= 9mm and -8mm of tasks] (task2) {WiFi};
            \node[module=1cm, below right= 3mm and 4mm of tasks] (task3) {\acs{can}};
            \node[module=1cm, below left= 3mm and 4mm of tasks] (task4) {Status};

            \node[fit=(task1) (task2) (task3) (task4) (freertos), draw, inner sep=2mm,label={[yshift=2mm, font=\sffamily]Řídicí jednotka}] (fitridici) {};
            % Connections
            \foreach \i in {1,2,3,4}
                \draw[->] (tasks)--(task\i);
            \draw[<->] (tasks)--(freertos);

            % WS
            \node[module, below=1.5cm of {task4.west|-fitridici.south}, anchor=north west] (api) {API};
            \node[module, below=of api] (php) {PHP};
            \node[module, below=of php] (mysql) {mySQL DB};
            \node[module, right= of php] (userweb) {Uživatelský \\panel};
            \node[fit={(php) (userweb) (api) (mysql) (mysql-|fitridici.west) (mysql-|fitridici.east) }, draw, inner xsep=\pgflinewidth, inner ysep=2mm, label={[yshift=2mm, font=\sffamily]Web server}] (fitWS) {};
            \draw[<->] (api)--(php);
            \draw[<->] (php)--(mysql);
            \draw[<->] (php)--(userweb);
        
            % perif
            \node[module, right=1.5cm of {task3-|fitridici.east}] (isr) {ISR};
            \node[module, right=3mm of isr.north east, anchor=north west] (can) {Obsluha\\\acs{can} příkazů};
            \node[module, above= 7mm of can.north east, anchor=south east] 
                (programloop) {Smyčka programu};
            \node[module, above=5mm of programloop] (dataprocess) {Zpracování dat};
            
            \node[fit={(can) (isr) (dataprocess|-fitridici.south) (dataprocess|-fitridici.north)}, draw, inner xsep=2mm, inner ysep=\pgflinewidth, label={[yshift=2mm, font=\sffamily]Periferie}] (fitperif) {};
            \node[module, right=1.5cm of dataprocess] (sensory) {Sensory};
            \draw[->] (isr)--(can);
            \draw[<->] (programloop)--(dataprocess);
            
            %arrow between boxes
            \draw[<->,dashed] (task2) to [out=-135,in=90] (api);
            \draw[->,dashed] (task3)--(isr);
            \draw[->,dashed] (can) to [out=-150,in=-45] (task3);
            \draw[<-,dashed] (dataprocess) -- (sensory);
        \end{tikzpicture}
        
        \caption{Zjednodušená architektura softwaru systému.}
        \label{fig:sw-blokove-schema}
    \end{figure}

    Jelikož jsou řídicí jednotka i periferie programovány ve stejném jazyce (C/C++), lze mezi nimi část kódu sdílet. Tímto způsobem lze částečně předejít chybám v~komunikaci modulů mezi sebou. Společná část kódu obsahuje definice datových typů a konstant používaných při komunikaci po sběrnici \acs{can}.  

\section{Popis \acs{can} komunikace}
    Protokol \acs{can} je poměrně rozsáhlý a velká část organizace komunikace je řešena přímo hardwarovou periferií mikrokontroléru. Pro úspěšnou a efektivní komunikaci je potřeba nastavit oba typy mikrokontrolérů stejně a stanovit společný standart komunikace. Systém popsaný v~této práci pracuje s~frekvencí \qty{125}{kHz} a používá standartní strukturu rámců s~identifikátorem zprávy dlouhým 11 bitů (standart \acs{can} 2.0B umožňuje také délku 29 bitů~\cite{PIC18F26Q83,esp32-tecnical-reference}). Struktura datového rámce je zobrazena na obr.~\ref{fig:obrazky/can-frame.png }. Sběrnice \acs{can} má implementovaný princip arbitrace, pokud začne komunikovat více zařízení současně, odešle se zpráva mající identifikátor s~nejvyšší prioritou. Logická nula se jeví na sběrnici jako dominantní, jednička naopak jako recesivní. Pokud zařízení odesílá recesivní signál a zároveň čte ze sběrnice signál dominantní, znamená to pro něj ztrátu arbitace a přestává vysílat, jelikož na sběrnici je v~danou chvíli vysíláná zpráva s~vyšší prioritou. Po skončení vysílání pak přerušené zařízení pokus opakuje.
    
        \begin{figure}[h!]
            \centering
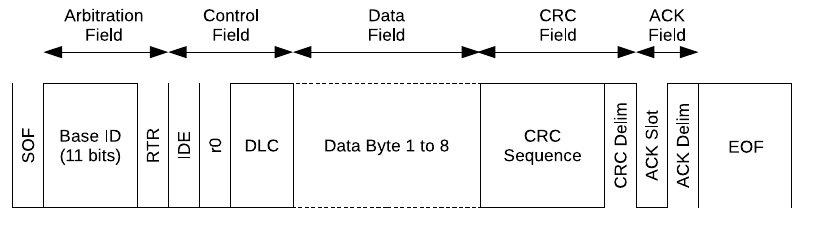
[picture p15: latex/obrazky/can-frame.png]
            
            \caption{Struktura datového rámce sběrnice \acs{can}. Převzato z~\cite{esp32-datasheet}}
            \label{fig:obrazky/can-frame.png   }
        \end{figure}

    V~navrženém systému nese identifikátor zprávy dvě informace. První tři odesílané bity značí typ zprávy. Rozlišena je zpráva určené všem jednotkám (BR -- Broadcast), zpráva od řídicí jednotky k~periferiím (TS -- master To Slave), od periferie zpět k~řídicí jednotce (TM -- slave To Master) a debug zpráva sloužící k~odeslání diagnostických dat nezávisle na ostatní komunikaci. Zbylých 8 bitů pak tvoří adresu jednotky odesílající zprávu (v~případě TM) resp. zprávu přijímající (v~případě TS). 
    
    \subsection{Adresace}
    Adresy jednotlivých modulů by měly být po startu systému nebo připojení nové jednotky automaticky přiděleny tak, aby nedošlo ke kolizi adres ani v~případě připojení několika sensorů stejného typu. Princip adresace spočívá v~sérii několika BR zpráv. Po startu systému pošle řídicí jednotka požadavek na adresaci, jako odpověď odešlou jednotky periferií své unikátní sériové číslo přičemž pouze jedna ze zpráv vyhraje arbitraci. Řídicí jednotka odpoví zprávou, která obsahuje sériové číslo úspěšné jednotky a přidělenou osmibitovou adresu. Následně zopakuje požadavek adresace a odpoví již pouze jednotky bez adresy, po dokončené adresaci pak neodpoví žádná jednotka. Pokud je do běžícího systému připojena nová periferie, odešle sama BR zprávu s~požadavkem na přidělení adresy.

    Ačkoliv je tento princip vymyšlen, v~rámci prototypu prozatím není implementován a otestován a každý typ periferie má pevně přidělenou adresu, lze tedy připojit pouze jednu periferii stejného typu. V~současné chvíli je toto řešení dostačující.

\section{Firmware řídicí jednotky}
    Firma Espressif nabízí pro své mikrokontroléry dva základní frameworky. Oba jsou vyvíjeny jako open-source a jsou tedy také volně dostupné pro jakékoliv použití. Univerzálním řešením vhodným i pro komerční aplikace je ESP-IDF (Espressif Integrated Development Framework). Pro hobby projekty lze využít také Arduino framework, který je taktéž oficiálně podporovaný. Poslední novinkou je pak možnost programování v~jazyce Rust namísto klasického C/C++, tento projekt je vytvářen komunitou uživatelů za podpory společnosti Espressif, prozatím ale nebyla oficiálně vydána stabilní verze. 

    V~rámci této práce je využit framework ESP-IDF spolu s~několika volně dostupnými knihovnami. Toto řešení již obsahuje HAL kód pro práci s~periferiemi MCU, není tedy potřeba pracovat přímo s~procesorovými registry. Framework má také podporu pro jednoduchý operační systém FreeRTOS, který je rovněž v~této práci využit~\cite{espressif-idf}. 

    \subsection{FreeRTOS}
        Systém FreeRTOS umožňuje vytvářet tzv. tasky neboli samostatné procesy které běží z~pohledu uživatele paralelně. Jelikož má zvolený mikroprocesor dvě jádra, mohou dva tasky běžet skutečně paralelně, více procesů se pak ve svém běhu střídá a běží tak přerušovaně, dá se říci pseudoparalelně. O~tuto režii se stará samotný operační systém a vývojář má několik možností, jak tento proces ovlivnit. V~případě vytížení procesoru systém přiděluje čas na základě nastavených priorit a dá přednost tasku s~vyšší prioritou, může se tak stát, že některý proces zůstane pozastaven na dlouhou dobu. Při tvorbě kódu je potřeba mít toto na paměti, vhodně zvolit priority tasků a také průběžně sledovat vytížení procesoru jednotlivými tasky.  

        Aby byl kód tzv. thread-safe, tedy bezpečný pro přístup z~více vláken, je potřeba ošetřit případy, kdy více tasků pracuje se stejnými daty nebo přistupuje ke stejné periferii mikrokontroléru. K~tomuto účelu FreeRTOS nabízí synchronizační objekty jako jsou mutexy, semafory případně fronty. 

    \subsection{Indikace stavu zařízení}
    \label{kap:indikace-stavu-ridici-jednoty}
        Šasi řídicí jednotky je vybaveno adresovatelným barevným \acs{led} páskem sestávajím ze čtyř diod jejichž úkolem je signalizovat uživateli stav zařízení. Jednotlivé stavy spolu s~popisem diod jsou zobrazeny na obr.~\ref{fig:stavove-led-mainboard}. Každý task, který je součástí procesu diagnostiky má svou vlastní globální proměnnou do které ukládá svůj stav. Dvakrát za vteřinu se pak spustí jednoduchá diagnostická funkce (běží v~rámci vlastního tasku). Ta jednotlivé stavové proměnné přečte, vyhodnotí celkový stav zařízení a aktualizuje barvu stavových \acs{led}. 
        \begin{figure}[h!]
            \centering
            \begin{tikzpicture}
                % Draw a rectangle
                \draw[thick] (0,0) rectangle (3*4,1);
                
                % Draw and fill four colorful circles
                \filldraw[fill=green,draw=black,thin]  (3*0.5, 0.5) circle (0.3) node[align=center,above=0.5] {\textbf{Stav zařízení}};
                \filldraw[fill=green,draw=black,thin]  (3*1.5, 0.5) circle (0.3) node[align=center,above=0.5] {\textbf{Stav WiFi}};
                \filldraw[fill=black,draw=black,thin]  (3*2.5, 0.5) circle (0.3) node[align=center,above=0.5] {\textbf{Alarm 1}};
                \filldraw[fill=black,draw=black,thin]  (3*3.5, 0.5) circle (0.3) node[align=center,above=0.5] {\textbf{Alarm 2}};

                % Draw and fill four colorful circles
                \filldraw[fill=blue,draw=black,thin]    (3*0.5, -1.5*0.8) circle (0.3) node[align=center,above=0.35] {Nedefinováno};
                \filldraw[fill=blue,draw=black,thin]    (3*1.5, -1.5*0.8) circle (0.3) node[align=center,above=0.35] {Nedefinováno};
                \filldraw[fill=blue,draw=black,thin]    (3*2.5, -1.5*0.8) circle (0.3) node[align=center,above=0.35] {Nedefinováno};
                \filldraw[fill=blue,draw=black,thin]  (3*3.5, -1.5*0.8) circle (0.3) node[align=center,above=0.35] {Nedefinováno};

                % Draw and fill four colorful circles
                \filldraw[fill=magenta,draw=black,thin] (3*0.5, -3.5*0.8) circle (0.3) node[align=center,above=0.35] {Inicializace};
                \filldraw[fill=magenta,draw=black,thin] (3*1.5, -3.5*0.8) circle (0.3) node[align=center,above=0.35] {Inicializace};
                \filldraw[fill=orange,draw=black,thin]  (3*2.5, -3.5*0.8) circle (0.3) node[align=center,above=0.35] {Upozornění};
                \filldraw[fill=orange,draw=black,thin]  (3*3.5, -3.5*0.8) circle (0.3) node[align=center,above=0.35] {Upozornění};

                % Draw and fill four colorful circles
                \filldraw[fill=green,draw=black,thin]   (3*0.5, -5.5*0.8) circle (0.3) node[align=center,above=0.35] {Ok};
                \filldraw[fill=orange,draw=black,thin]  (3*1.5, -5.5*0.8) circle (0.3) node[align=center,above=0.35] {Připojeno};
                \filldraw[fill=red,draw=black,thin]   (3*2.5, -5.5*0.8) circle (0.3) node[align=center,above=0.35] {Alarm};
                \filldraw[fill=red,draw=black,thin]  (3*3.5, -5.5*0.8) circle (0.3) node[align=center,above=0.35] {Alarm};

                % Draw and fill four colorful circles
                \filldraw[fill=red,draw=black,thin]     (3*0.5, -7.5*0.8) circle (0.3) node[align=center,above=0.35] {Chyba};
                \filldraw[fill=green,draw=black,thin]   (3*1.5, -7.5*0.8) circle (0.3) node[align=center,above=0.35] {Online};
                \filldraw[fill=black,draw=black,thin]   (3*2.5, -7.5*0.8) circle (0.3) node[align=center,above=0.35] {OK};
                \filldraw[fill=black,draw=black,thin]   (3*3.5, -7.5*0.8) circle (0.3) node[align=center,above=0.35] {OK};

                % Draw and fill four colorful circles
                \filldraw[fill=red,draw=black,thin]     (3*1.5, -9.5*0.8) circle (0.3) node[align=center,above=0.35] {Chyba};
            \end{tikzpicture}
            
            \caption{Stavové \acs{led} řídicí jednotky.}
            \label{fig:stavove-led-mainboard}
        \end{figure}

    \subsection{Popis jednotlivých tasků}
        Řídicí jednotka vykonává současně několik funkcí. Komunikuje s~periferiemi skrze sběrnci CAN, ovládá připojená relé a stavové diody, kromě toho také komunikuje s~webovým serverem prostřednictvím WiFi. Jednotlivé úlohy je třeba vykonávat periodicky, ovšem každou s~jinou prioritou. Kód je proto rozdělen do několika tasků podle své funkce a priority. 

        K~synchronizaci tasků jsou využity binární semafory. K~převzetí semaforu ve {FreeRTOS} slouží funkce \texttt{xSemaphoreTake( xSemaphore, xBlockTime )}. Na řádku s~touto funkcí kód čeká až do přijetí semaforu odeslaného jiným taskem nebo do vypršení času stanoveného druhým parametrem. 

        Každý z~tasků začíná inicializací, kdy se jednorázově nastaví potřebné proměnné. Dále pokračuje nekonečnou smyčkou přerušenou vždy čekáním na semafor nebo neblokujícím zpožděním za pomocí funkce \texttt{vTaskDelay( const TickType\_t xTicksToDelay )}.

        % \begin{lstlisting}[language={[LaTeX]TeX}]
        %     \section{Balíček lstlistings}
        %     Pro vysázení zdrojových souborů je možné použít
        %         balíček \href{https://www.ctan.org/pkg/listings}%
        %         {\texttt{listings}}.
        %     Balíček zavádí nové prostředí \texttt{lstlisting} pro
        %         sazbu zdrojových kódů.
        %     \end{lstlisting}
        
        \subsubsection{Kontrolní proces -- \texttt{control\_task}}
            Jedná se o~hlavní task programu co se týče samotného algoritmu. Na začátku běhu ve vhodném pořadí spustí ostatní tasky a provede vlastní inicializaci. Je spuštěna adresace zařízení na sběrnici CAN a od připojených periferií následně vyžádána informace o~jejich typu, sériovém čísle a současnému stavu. Z~perzistentní paměti flash je na základě sériového čísla načtena konfigurace jednotlivých modulů a samotného systému. 

            Ve smyčce je následně pravidelně prováděn sled několika operací. Pokud je to potřeba, dojde ke stažení nové konfigurace ze serveru, aktualizaci odpovídajích proměnných i paměti flash.  O~nutnosti této operace rozhoduje \texttt{wifi\_task}.

            Dále jsou obslouženy periferie na sběrnici. Je vyžádán jejich status a dle typu také senzorická a provozní data. 

            Na základě konfigurace systému, získaných dat a reálného času je odeslán požadavek odpovídajícím akčím členům a aktualizován stav relé. Také je zpracován případný alarm, který je následně jiným taskem signalizován prostřednictvím stavových diod. 

            Dle nastavené periody jsou data získaná ze senzorů také odeslána na webový server.

        \subsubsection{Obsluha WiFi --  \texttt{wifi\_task}}
            V~inicializační fázi tohoto tasku je vznešen požadavek na připojení k~síti WiFi. V~případě selhání nebo pozdějšího odpojení je pokus automaticky opakován. 
            
            V~nekonečné smyčce pak task periodicky kontroluje dostupnost internetového připojení, dotazuje se serveru na poslední dostupnou verzi konfigurace a aktualizuje údaj o~reálném čase (ten je následně uchován vnitřním \acs{rtc} časovačem mikrokontroléru).

        \subsubsection{Obsluha sběrnice CAN --  \texttt{can\_bus\_task}}
            Inicializuje potřebné GPIO piny a připraví potřebné proměnné. Ve smyčce pak pravidelně kontroluje příchozí zprávy na sběrnici (zejména typu Broadcast, které mohou být odeslány periferiemi bez vyzvání). Příchozí zprávy filtruje a pomocí front předává dalším taskům. Na začátku vždy čeká na kontrolní semafor značící požadavek na vyčtení sběrnice. Pokud není vyslán požadavek, čekání na semafor vyprší a sběrnice je zkontrolována s~danou periodou.

        \subsubsection{Indikace stavu --  \texttt{status\_update\_task}}
            Zpracovává stavové proměnné ostatních tasků a na základě těchto dat vyhodnocuje stav zařízení. Tento stav následně indikuje za pomoci stavových diod, jak bylo popsáno v~kapitole~\ref{kap:indikace-stavu-ridici-jednoty}.

\section{Firmware periferií}
    Jak bylo popsáno v~kapitole~\ref{sec:modul-periferie}, všechny periferie mají stejné jádro. Ve všech pracuje stejný mikrokontrolér (PIC18F26), stejným způsobem pracují se sběrnicí CAN a také část příkazů na sběrnici je všem periferiím společná. Rozdíl mezi periferiemi je daný pouze připojenými sensory. Ty vyžadují vždy specifické nastavení vstupních a výstupních pinů, zpracování dat a jejich odeslání skrze sběrnici CAN. 

    Tato struktura je replikována také ve zdrojovém kódu. Pro všechny periferie existuje společný projekt, kdy základní kód zůstává vždy stejný. Pro sestavení a nahrání programu do konkrétního modulu je potřeba upravit hlavičkový soubor \texttt{device\_type.h}. Tento soubor nastaví typ zařízení a následně za pomoci preprocesorových direktiv vloží do projektu pouze odpovídající knihovny. Výňatek z~tohoto souboru je zde uveden jako výpis~\ref{lst:devicetype}. Stejným principem je kód větven na všech místech, kde je toto potřeba. 

    Program sestává ze dvou hlavních částí. Nejprve je to fáze incializace, kdy dojde k~nastavení potřebných registrů a proměnných. Poté zařízení vstupuje do nekonečné smyčky. V~té jsou periodicky vyčítána data z~připojených senzorů resp. ovládány akční členy.  Příchozí zprávy na sběrnici CAN vyvolají vždy přerušení, zpracovávají se tedy mimo hlavní smyčku programu. 

\clearpage % TODO zarovnat dle zbytku
\begin{lstlisting}[frame=single,caption={Část souboru \texttt{device\_type.h} sloužící k~výběru typu cílené periferie.},label=lst:devicetype,basicstyle=\ttfamily\small, keywordstyle=\color{black}\bfseries\underbar,]
#ifndef DEVICE_TYPE_H
#define	DEVICE_TYPE_H

// soubor procesoru PIC
#include <xc.h>   

// knihovna sdílená s~řídicí jednotkou
#include "../shared/common_types.h" 

// Výběr jedné z~hodnot definovaných v~common_types.h
#define DEVICE_TYPE     DEVICE_TYPE_WATER_LEVEL_SENSOR

...

// Hlavičkové soubory specifické dle typu periferie
#if DEVICE_TYPE == DEVICE_TYPE_LED_BOARD
    #include  "led_board_driver/led_board_driver.h"
#elif DEVICE_TYPE == DEVICE_TYPE_TEMP_SENSOR
    #include "temp_sensor_driver/temp_sensor_driver.h"
#elif DEVICE_TYPE == DEVICE_TYPE_WATER_LEVEL_SENSOR
    #include "water_level_driver/water_level_driver.h"
...
#else
    #error "Not supported DEVICE_TYPE"
#endif
#endif	/* DEVICE_TYPE_H */
\end{lstlisting}

\subsection{Zpracování příkazů CAN}
    Jako základ je využit kód vytvořený modulem Microchip Code Configurator. Jedná se o~užitečný nástroj, který předpřipraví kód nutný k~nastavení konkrétních registrů. Také obsahuje funkce úrovně HAL, aby nebylo nutné dále pracovat přímo s~registry. Vygenerovaý kód je přitom krátký a snadno čitelný. Veškeré generované nastavení bylo následně kontrolováno s~katalogovým listem procesoru a v~případě potřeby upraveno. 

    Na rozdíl od procesoru řídicí jednotky, PIC18F26 obsahuje v~periferii CAN až 11 různých filtrů příchozích zpráv~\cite{PIC18F26Q83}. Již na úrovni hardwaru jsou tak zprávy rozděleny dle typu. Zprávy určené periferiím (TS - To Slave) jsou řazeny do jedné fronty, zprávy určené všem (BR - Broadcast) pak do druhé fronty. Ostatní zprávy nejsou zpracovány vůbec. Při přijetí zprávy je vyvoláno přerušení a kód přečte zprávu z~dané fronty. Pokud je to potřeba, odešle vlastní zprávu jako odpověď. První bajt datového pole zprávy vždy identifikuje daný příkaz. V elektronické příloze této práce se také nachází dokument, kde je struktura jednotlivých příkazů rozpracována podrobněji.

\subsection{Smyčka programu}
    Jelikož zpracování příkazů ze sběrnice CAN probíhá vždy jako obsluha přerušení, samotná smyčka programu je velmi jednoduchá.  V~případě sensorů ji lze rozdělit do tří kroků. Nejprve jsou vyčtena surová data ze sensorů a uložena do vhodných proměnných. Ve druhém kroku jsou data zpracována -- je vyhodnocena jejich správnost, provedena korekce nebo přepočet, případně jsou data průměrována z~více opakování měření. Ve třetím kroku jsou zpracovaná data uložena do globální promměnné. Pokud přišel po sběrnici CAN požadavek na odeslání dat, jsou mu předána tato data. 

    Na konci smyčky je pak vždy vyhodnocen stav zařízení a opět uložen do globální proměnné.

    Přesný průbeh jednotlivých kroků programové smyčky se liší v~závislosti na typu periferie a byl upravován průběžně k~dosažení optimální funkce jednotlivých sensorů.

\clearpage
\section{Webové rozhraní}
    Aby bylo možné systém konfigurovat a monitorovat, bylo zapotřebí navrhnout a vytvořit webové rozhraní. Důležitým krokem v~rozhodování byla volba, zda bude \acs{mcu} řídicí jednotky sloužit přímo jako webový server nebo pouze jako klient. První scénář klade podstatně vyšší nároky na zatížení a paměť \acs{mcu}, výhodou je ale velmi jednoduchý systém, který funguje samostetně bez nutnosti externího serveru případně také bez připojení k~internetu (ESP32 může sloužit přímo jako přístupový bod). Výhodou druhé varianty je větší flexibilita, externí server má nesrovnatelně vyšší výkon a kapacitu úložiště a umožní tak tvorbu mnohem komplexnější webové stránky, která bude (v~případě připojení serveru do internetu) dostupná odkudkoliv. Server zároveň může ukládat měřená data a ta tedy budou dostupná i v~případě, že samotné zařízení je mimo provoz nebo není připojeno k~síti.

    V~rámci realizace této práce byla zvolena varianta externího serveru. Jádro vytvořené webové aplikace tvoří program v~jazyce PHP, který zpracovává jak požadavky uživatele, tak i samotného zařízení. Na pozadí dále běží databázový server s~otevřeným systémem MySQL, sloužící k~uchování provozních dat. V~databázi jsou uloženy údaje o~uživatelích, systémech akvárií (tedy řídicí jednotka a k~ní připojené periferie) a jejich konfiguraci. Také jsou zde ukládána data ze senzorů. V~záznamu odpovídajícímu danému systému akvária je uložen číselný údaj o~aktuální verzi konfigurace. Pokud uživatel změní některé nastavení, toto číslo se inkrementuje. Na verzi konfigurace se zařízení pravidelně dotazuje a v~případě změny si následně ze serveru stáhne celou novou konfiguraci.

    \subsection{API rozhraní -- komunikace z~pohledu zařízení}
    Zařízení komunikuje s~webem pomocí aplikačního rozhraní (API), které tvoří nenáročný způsob komunikace využívající formát JSON. Jednotlivé adresy API rozhraní jsou přehledně popsány v~tab.~\ref{tab:prehled-api-adres}. 

    \begin{table}[h]
        \centering
        \caption{Přehled adres aplikačního rozhraní.}
        \label{tab:prehled-api-adres}
        \begin{tabular}{|l|l|l|l|}
            \hline
            Adresa & Funkce & Odchozí data\(^{*}\)  & Příchozí data\(^{*}\)  \\ \hline\hline
           
            /ping & Kontrola dostupnosti & - & -  \\ \hline
            /ping?SN= & Kontrola konfigurace & Sériové číslo & Verze konfigurace  \\ \hline
            /config/get?SN= & Stažení konfigurace & Sériové číslo & Plná konfigurace  \\ \hline
            /data/add & Odeslání dat & Provozní data & -  \\ \hline
            /data/view & Načtení dat & - & Data pro zobrazení na webu  \\ \hline
                            %     & S &  &  & A  \\ \hline
                            %     & S &  &  & A  \\ \hline
                            %     & S &  &  & A  \\ \hline
                            %     & S &  &  & A  \\ \hline
                            %     & S &  &  & A  \\ \hline
                            %     & S &  &  & A  \\ \hline
                            %     & S &  &  & A  \\ \hline
            \end{tabular}
            \begin{tabular}{c}
                \(^{*}\)Z pohledu  řídicí jednotky.
            \end{tabular}   
    \end{table}

    \subsection{Uživatelská aplikace}
        Z~pohledu uživatele je možnost se na webu registrovat a přihlásit. Teprve po přihlášení je zobrazeno grafické menu. Webová aplikace slouží dvěma hlavním funkcím, kterým odpovídají také položky menu. 
        
        \begin{figure}[h!]
            \centering
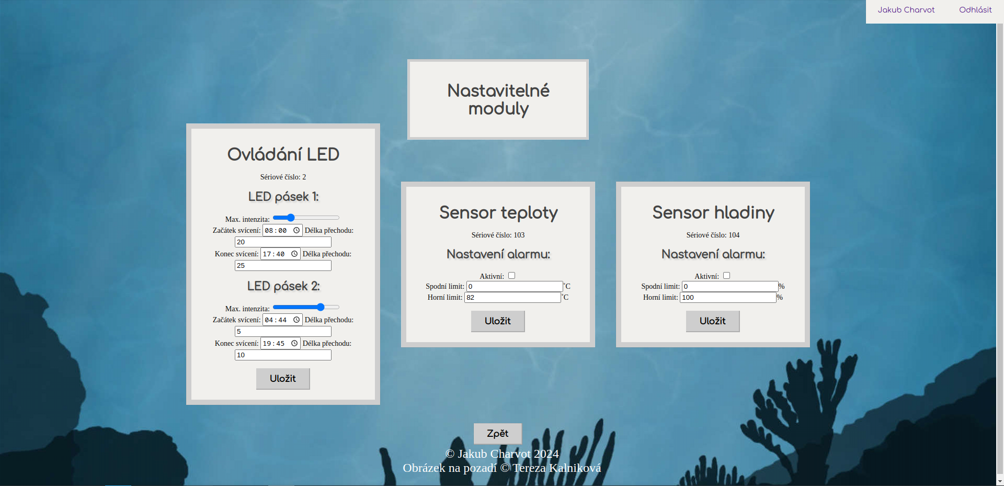
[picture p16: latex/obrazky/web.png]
            
            \caption{Ukázka jedné ze stránek webové aplikace.}
            \label{fig:obrazky-web.png}
        \end{figure}
        
        První položkou je zobrazení stavu zařízení. Kliknutí na odkaz přivede uživatele na podstránku zobrazující grafy všech dostupných dat jeho akvarijního systému. V~grafech je v~tuto chvíli zobrazeno vždy 100 posledních hodnot. 

        Druhá položka je nazvaná jako \uv{Scénáře} a nachází se v~ní konfigurace systému a nastavení jednotlivých modulů. Pro sensory lze nastavit úrovně, které má systém vyhodnotit jako alarmující. Pro každou síťovou zásuvku je pak možné přepnout mezi dvěma režimy. V~manuálním režimu uživatel přímo nastaví sepnutí nebo rozepnutí zásuvky, druhým režimem je pak časovač, kdy lze nastavit pravidelné časy vypnutí a zapnutí.

        Pro představu o~vzhledu webu je zde přiložen obr.~\ref{fig:obrazky-web.png}, v~elektronické příloze je pak snímků více.

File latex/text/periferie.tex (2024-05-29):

\chapter{Volba a návrh periferií}
    Tato kapitola se již věnuje návrhu konkrétních periferií, tedy jednotlivých senzorů a akčních členů. Po technické stránce jsou všechny zmíněné moduly nadstavbou pro \uv{obecný modul periferie} popsaný detailně v~předešlé kapitole. Jelikož je celý systém modulární, je pravděpodobné, že postupem času bude dále rozšiřován o~nové typy periferií a i v~současné chvíli je jich v~plánu více, než je v~možnostech této práce. Pro lepší přehlednost se v~tab.~\ref{tab:prehled-periferii} nachází přehled všech realizovaných i v~tuto chvíli pouze plánovaných periferií.

    \begin{table}[h]
        \centering
        \caption{Přehled periferií.}
        \label{tab:prehled-periferii}
        \begin{tabular}{|l|l|l|l|l|}
            \hline
            Název & Typ & Napájení & Funkce & Realizováno \\ \hline\hline
            Sensor teploty  & S~& \qty{5}{V}    & Teplota vody                       & Ano, kap.~\ref{sec:perif-sensor-teploty}  \\ \hline
            Sensor hladiny  & S~& \qty{5}{V}    & Výška hladiny (spojitě + skokově)  & Ano, kap.~\ref{sec:perif-sensor-hladina}  \\ \hline
            \acs{led} osvětlení   & A~& \qty{24}{V}   & Intenzita osvětlení                & Ano, kap.~\ref{sec:perif-led-osvetleni}  \\ \hline
            Sensor \acs{ph}       & S~& \qty{5}{V}    & \acs{ph} vody                            & Ne, kap.~\ref{sec:perif-sensor-ph}  \\ \hline
            Topné těleso    & A~& \qty{230}{V}  & Ohřev vody                         & Ano, kap.~\ref{sec:perif-230v}  \\ \hline
            Filtr vody      & A~& \qty{230}{V}  & Filtrace vody                      & Ano, kap.~\ref{sec:perif-230v}  \\ \hline
            Krmítko         & A~& \qty{24}{V}   & Dávkování krmiva                   & Ne  \\ \hline
            Sensor průtoku  & S~& -             & Voda tekoucí filtrem               & Ne  \\ \hline
                            % & S &  &  & A  \\ \hline
                            %     & S &  &  & A  \\ \hline
                            %     & S &  &  & A  \\ \hline
                            %     & S &  &  & A  \\ \hline
                            %     & S &  &  & A  \\ \hline
                            %     & S &  &  & A  \\ \hline
                            %     & S &  &  & A  \\ \hline
                            %     & S &  &  & A  \\ \hline
                            %     & S &  &  & A  \\ \hline
            \end{tabular}
            \begin{tabular}{c}
                S~= sensor, A~= akční člen \\
            \end{tabular}
   
    \end{table}

\input{text/periferie/sensor_teploty.tex}

\input{text/periferie/vyska_hladiny.tex}

\input{text/periferie/led_modul.tex}

\section{Senzor \acs{ph}}
\label{sec:perif-sensor-ph}
Kapitola~\ref{sec:monitorovani} stručně popisuje význam měření pH vody v~akváriu. Ačkoliv informace o~pH vody může být velmi užitečná, lze konstatovat, že kontinální měření této veličiny není pro provoz akvária nutností. Vývoj této periferie proto neměl v~rámci práce nejvyšší prioritu a z~důvodu nedostatku času nakonec nebyla realizována.

Nejjednodušším způsobem nepřetržitého měření je použití pH sondy. V~rámci této práce byla zvolena elektrochemická sonda E201, kterou je možno vidět na obr.~\ref{fig:obrazky-foto-ph_sonda-jpeg}. Sonda se kládá ze dvou elektrod, referenční a měřicí. Měřicí elektroda je umístěna ve skleněném pouzdře opatřeném iontově sensitivní úpravou. Elektroda reaguje na kationty vodíku H+, které přímo souvisí s~pH měřeného roztoku. Princip měření je potenciometrický. Referenční elektroda generuje stabilní potenciál, naopak na elektrodě měřicí vzniká potenciál závislý na pH roztoku. Potenciálový rozdíl je pak měřitelný dalšími obvody. Pro korektní převod měřené hodnoty je potřeba sensor kalibrovat. Jednoduchou kalibraci lze provést vložením sondy do dvou roztoků známého pH a následným proložením měřených hodnot kalibrační přímkou. K~vytvoření kalibračních roztoků se využívá speciálních prášků, které lze zakoupit spolu se samotnou sondou.

\begin{figure}[h!]
    \centering
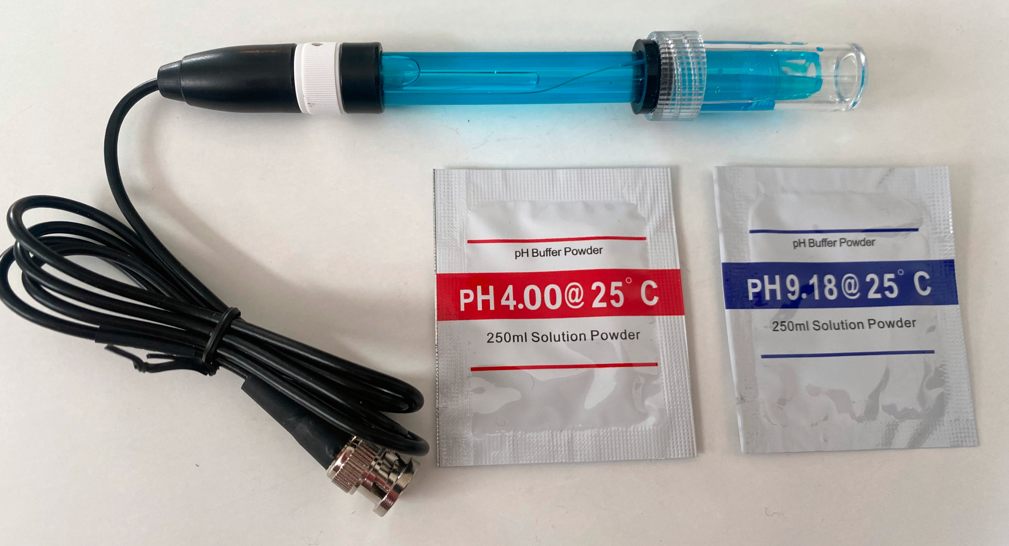
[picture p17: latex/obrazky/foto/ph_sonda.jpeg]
    
    \caption{pH sonda E201 spolu s~kalibračními prášky.}
    \label{fig:obrazky-foto-ph_sonda-jpeg}
\end{figure}

Z~hlediska mikrokontroléru je zapotřebí periferie ADC (analogově digitální převodník). Použitý PIC18F26 je vybaven převodníkem s~rozlišením  12 bitů, což je pro danou aplikaci více než dostatečné. Aby samotný sensor nebyl příliš proudově zatížen, bude pravděpodobně nutné přidat mezi sensor a mikrokontrolér ještě operační zesilovač. 

\input{text/periferie/230v.tex}

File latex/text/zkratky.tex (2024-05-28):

\cleardoublepage
\chapter*{\listofabbrevname}
\phantomsection
\addcontentsline{toc}{chapter}{\listofabbrevname}

\begin{acronym}[iotasdasdsd]

	\acro{iot}[IoT]{Internet of Things -- internet věcí}

	\acro{led}[LED]{Light-Emitting Diode -- dioda emitující světlo}
	\acro{ph}[pH]{Potential of Hydrogen -- potenciál vodíku}
	\acro{co2}[CO\textsubscript{2}]{Carbon Dioxide -- oxid uhličitý}
	\acro{pc}[PC]{Personal Computer -- osobní počítač}
	\acro{wifi}[Wi-Fi]{Wireless Fidelity -- známá bezdrátová síť}
	\acro{spi}[SPI]{Serial Peripheral Interface -- typ sběrnice}
	\acro{i2c}[I\textsuperscript{2}C]{Inter-Integrated Circuit -- typ sběrnice}
	\acro{dps}[DPS]{deska plošných spojů}
	\acro{can}[CAN]{Controller Area Network -- typ sběrnice}
	\acro{cs}[CS]{Chip Select -- signál patřící k~SPI sběrnici}
	\acro{uart}[UART]{Universal Asynchronous Receiver-Transmitter -- typ sběrnice}
	\acro{mcu}[MCU]{Microcontroller Unit -- mikrokontrolér}
	\acro{dc}[DC]{Direct Current -- stejnosměrný proud}
	\acro{mosfet}[MOSFET]{Metal-Oxide-Semiconductor Field-Effect -- typ unipolárního tranzistoru}
	\acro{esd}[ESD]{Electrostatic Discharge -- elektrostatický výboj}
	\acro{vcc}[VCC]{Voltage at the Common Collector -- symbol pro kladné napájecí napětí}
	\acro{vdd}[VDD]{Voltage Drain Drain -- symbol pro kladné napětí zařízení}
	\acro{pptc}[PPTC]{Polymeric Positive Temperature Coefficient -- také značí typ vratné pojistky}
	\acro{gpio}[GPIO]{General Purpose Input/Output -- označení vstupně výstupních pinů MCU}
	\acro{sda}[SDA]{Serial Data Line -- datový signál pro \acs{i2c}}
	\acro{scl}[SCL]{Serial Clock Line -- hodinový signál pro \acs{i2c}}
	\acro{oled}[OLED]{Organic Light-Emitting Diode -- často používaný typ displeje}
	\acro{pwm}[PWM]{Pulse-Width Modulation -- pulzně šířková modulace}
	\acro{adc}[ADC]{Analog to Digital Convertor -- Analogově-digitální převodník}
	\acro{dac}[DAC]{Digital to Analog Convertor -- Digitálně-analogový převodník}
	\acro{vcc}[VCC]{Voltage Common Collector -- napájecí napětí}
	\acro{gnd}[GND]{Ground -- zem, zemnicí vodič}
	\acro{esr}[ESR]{Equivalent Series Resistance -- ekvivalentní sériový odpor}
	\acro{ntc}[NTC]{Negative Temperature Coefficient -- záporný teplotní koeficient}
	\acro{ptc}[PTC]{Positive Temperature Coefficient -- kladný teplotní koeficient}
	\acro{esp-idf}[ESP-IDF]{Espressif IoT Development Framework -- vývojový framework firmy Espressif}
	\acro{hal}[HAL]{Hardware Abstraction Layer -- abstrakční vrstva ve zdrojovém kódu}
	\acro{api}[API]{Application Programming Interface -- aplikační rozhraní}
	\acro{rtos}[RTOS]{Real-Time Operating System -- operační systém reálného času}
	\acro{php}[PHP]{PHP Hypertext Preprocessor -- programovací jazyk}
	\acro{isr}[ISR]{Interrupt Service Routine -- obsluha přerušení}
	\acro{db}[DB]{Database -- databáze}
	\acro{emc}[EMC]{Elektro magnetická kompatibilita}
	\acro{json}[JSON]{JavaScript Object Notation -- formát ukládání a přenosu strukturovaných dat}
	\acro{rtc}[RTC]{Real Time Clock -- označení reálného času}

\end{acronym}

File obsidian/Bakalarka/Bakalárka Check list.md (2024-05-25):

- Study:
	- RTOS: [[freeRTOS notes]]

- Úprava textu před finálním odevzdáním
- TODO:
	- Kontrola citací - jednotný styl pro stejný typ citací
	- Obrázky nesmí být na konci kapitoly ani strany
	- Nesmí býti prázdná kapitola
	- vlna - neboli jednopísmenková slova na konci řádků
	- Zkratky
	-  Sjednotit značení součástek buď U_1 nebo U1

- Obrázky k doplnění:
	- foto relé v krabici
	- Foto sensorů - teplota, hladina, led board, pH

- při textu pozor
	- diplej
	- D-sub
	- řídicí
	-  BUCK malým
	- kontrolér

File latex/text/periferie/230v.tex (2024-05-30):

\section{Ovládání 230V periferií}
\label{sec:perif-230v}
Jak vyplývá z~požadavků zařízení a přehledu používané akvaristické techniky, pro automatizovaný provoz akvária je nutné umožnit řídicí jednotce ovládat několik okruhů se síťovým napětím a spínat tak zvlášť zakoupené hotové spotřebiče pracující s~tímto napětím. Jedná se typicky o~ohřev vody, filtraci, popř. některé druhy osvětlení. 

\begin{figure}[h!]
    \centering
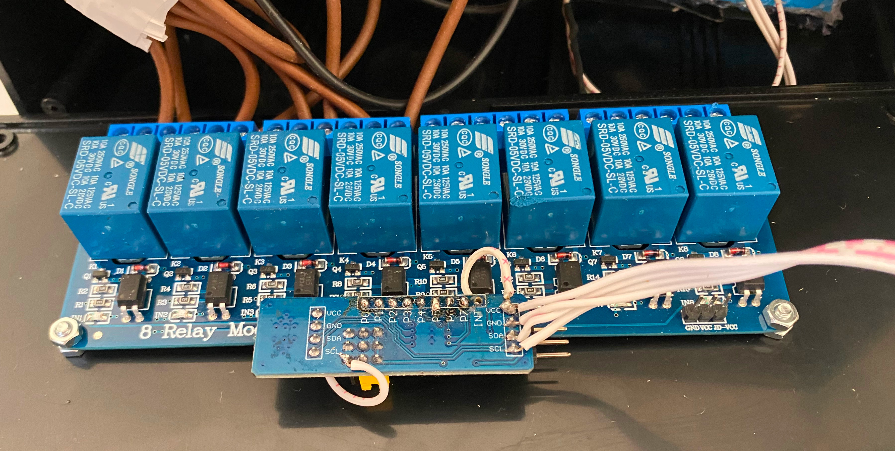
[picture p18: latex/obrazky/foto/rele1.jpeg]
    
    \caption{Relé modul spolu s~expandérem pinů.}
    \label{fig:obrazky-230-rele-jpg}
\end{figure}

Aby uživatel mohl spínaná zařízení bezpěčně připojit bez nutnosti odborné způsobilosti, nachází se na hlavním šasi zařízení čtyři standartní zásuvky (typ E) s~jednofázovým napětím \qty{230}{V}. Fázové vodiče jsou uvnitř zařízení přerušeny spínacími relé. Je použit předpřipravený modul disponující osmi relé~\cite{eshop-laskakit-rele}, čtyři z~nich tedy zůstanou nevyužité a slouží jako rezerva pro případ poškození některého z~používaných relé nebo při potřebě budoucího rozšíření o~další zásuvky. 

\begin{figure}[h!]
    \centering
    % trim=left bottom right top
    \includegraphics
    [
        width=0.8\textwidth, 
        page=3, 
        trim=2.5cm 14.5cm 18cm 1.5cm, 
        clip
    ]{obrazky/exportovane/ukazky-do-textu.pdf}
    \caption{Schéma jednoho kanálu relé modulu. Vytvořeno v~KiCad 7.0.}
    \label{fig:relay-board-simp-schema}
\end{figure}

Z~důvodu nedostatku pinů na mikrokontroléru řídicí jednotky (ESP32) je k~relé modulu připojen ještě jeden externí modul, a to expandér \acs{gpio} pinů komunikující přes sběrnici \acs{i2c}~\cite{eshop-laskakit-expander}. Z~pohledu mikrokontroléru jsou tak všechny zásuvky ovládány pomocí dvou \acs{gpio} pinů (\acs{sda}, \acs{scl}). Ty je navíc možné dále využít pro připojení jiných periferií jako např. O\acs{led} displaje pro zobrazení stavu zařízení.

Relé na použitém modulu potřebuje pro spolehlivé sepnutí napětí alespoň \qty{5}{V}, logické signály řídicí jednotky ale pracují s~napětím pouze \qty{3.3}{V}. Ze schématu na obr.~\ref{fig:relay-board-simp-schema} je vidět, že použitý relé modul je spínán signálem logické nuly, tímto způsobem je problém s~rozdílnou úrovní napájení elegantně vyřešen. 

Do budoucna by bylo možným zlepšením a rozšířením této práce zahrnutí obou zmíněných modulů přímo na \acs{dps} řídicí jednotky.

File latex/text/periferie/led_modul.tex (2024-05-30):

\section{\acs{led} osvětlení}
\label{sec:perif-led-osvetleni}

    Úkolem této periferie je zajistit osvětlení akvária a umožnit jeho ovládání. V~porovnání s~ostatními moduly je zapojení relativně komplexní a proto byla pro tuto periferii navržena a zhotovena vlastní \acs{dps} (fungující jako dceřinná deska, viz.~\ref{sec:modul-periferie}). Jako typ svítidla byly zvoleny \acs{led} pásky pracující s~napětím \qty{12}{V}. Modul musí být schopen samostatně ovládat 2 \acs{led} pásky, kdy za pomocí regulace proudu do \acs{led} pásku nastaví intenzitu osvětlení. 

\subsection{Návrh zapojení}
    Na začátku návrhu je potřeba specifikovat si požadavky na elektrické parametry zapojení. Uvažujme délku každého pásku \(l=\qty{1}{m}\), vstupní napětí získané z~konektoru D-sub \(U_{in} =\qty{24}{V}\) a výstupní napětí pro které je pásek určen \(U_{out} =\qty{12}{V}\). Pro stanovení maximálního proudu bylo vycházeno z~údajů na e-shopu \acs{led} Solution~\cite{eshop-ledsolution-svetlo}, kdy nejvýkonější nabízený \acs{led} pásek pro dané napětí má příkon \(P_{i}= \qty{20}{W/m}\). Pak každý kanál musí být schopen dodat proud odpovídající nejnáročnějšímu scénáři:
    \begin{equation}  
        I_{max} = \frac{P_{i}\cdot l }{U_{out}} = \frac{20\cdot 1 }{12} = \qty{1.66}{A}
    \end{equation}

    Jelikož se jedná o~dceřinnou desku pro obecný modul, rozměr výsledné \acs{dps} je omezen a část plochy je navíc využita konektory pro vsazení do obecného modulu. Je tedy potřeba zvolit co nejvíce integrované řešení, které současně slibuje dobrou účinnost a tedy co nejnižší ohřev zařízení během provozu.

    Pro řízení \acs{led} osvětlení je často používán proudový zdroj, který umožňuje lineárně regulovat výstupní proud a tím i intenzitu osvětlení. Na trhu existuje opět celá řada čipů určena přímo k~ovládání \acs{led} pásků~\cite{TI_LED_Drivers}, problém je zde ale v~tom, že uživatel velmi pravděpodobně připojí pásek s~nižším, předem neznámým příkonem. Maximální proud je tedy specifický danému \acs{led} pásku a proudový zdroj by musel zároveň spolehlivě zaručit, že nebude překročeno napětí \(U_{out} =\qty{12}{V} \).

    \begin{figure}[h!]
        \centering
        % trim=left bottom right top
        \includegraphics
        [
            width=\textwidth, 
            page=1, 
            trim=2.5cm 11.5cm 16cm 1.5cm, 
            clip
        ]{obrazky/exportovane/ukazky-do-textu.pdf}
        \caption{Zjednodušené schéma ovladače \acs{led}. Vytvořeno v~KiCad 7.0.}
        \label{fig:led-board-simp-schema}
    \end{figure}
    
    Touto funkcí většina čipů nedisponuje a pokud ano, nejsou dostatečně integrované pro použití v~této aplikaci. Po důkladné rešerši a několika iteracích návrhu se nakonec jeví jako nejlepší možnost použití napěťového měniče typu buck spolu se zesilovačem pro snímání proudu. Snímaný proud je následně zpracován mikrokontrolérem a jsou upraveny poměry ve zpětné vazbě měniče, aby napětí odpovídalo požadovanému proudu.

\subsubsection{Popis schématu a výpočty hodnot součástek}
    Zjednodušené schéma pro jeden ovládaný kanál se nachází na obr.~\ref{fig:led-board-simp-schema}, při výpočtech bude použito označení součástek z~tohoto schématu. Úplné schéma modulu pak lze nalézt v~příloze~\ref{priloha:schema-led-board}.

    Jako buck kontrolér je zvolen čip AP63356Q vyvinutý společností Diodes incorporated, jedná se o~úspornou a velmi malou součástku, která v~sobě integruje oba potřebné MOSFET tranzistory a spíná s~pevně danou frekvencí \(f_{SW}=\qty{450}{kHz} \) ~\cite{Diodes_AP63356Q}. Pro snímání proudu poslouží čip INA180A4 firmy Texas Instruments~\cite{TI_INA180A4}.

    Z~obrázku je vidět, že pro ovládání jednoho kanálu \acs{led} pásků jsou využity 4 piny \acs{mcu}. RA4 a RB1 fungují jako vstupy, RA2 a RA3 pak jako výstupy. Rezistor \(R_{1}\) drží buck měnič ve vypnutém stavu, dokud mikrokontrolér nenastaví hodnotu pinu RA2 na logickou 1. Pin RA4 je pak čipem (U1) stažen k~zemi vždy, když na výstupu není odpovídající nastavené napětí.  
    
    Nastavení výstupního napětí měniče je dosaženo za pomoci zpětnovazební smyčky mezi výstupním uzlem (I.) a zpětnovazebním pinem FB (uzel II.). V~uzlu II. je drženo konstantní napětí \qty{0.8}{V}~\cite{Diodes_AP63356Q}, poměrem rezistorů R3 a R4 je pak definováno výstupní napětí. Zvolíme hodnotu odporu \(R_{4} = \qty{10}{k\ohm}\), pro maximální požadované napětí \(U_{outMAX} = \qty{12}{V}\) platí:
    \begin{equation}
        R_{3} = R_{4}\cdot \left(\frac{U_{outMAX} }{\num{0.8}}-1\right) = \qty{10}{k}\cdot \left(\frac{12}{\num{0.8}}-1\right) = \qty{140}{k\ohm}
    \end{equation} 
    Na pin RA3 mikrokontroléru je přivedeno analogové napětí z~periferie \acs{dac} popř. \acs{pwm} signál. Skrze rezistor R5 (a ochrannou diodu) pak teče proud do rezistoru R4, úbytek napětí na tomto rezistoru je ale konstantní (\qty{0.8}{V}) a tedy je konstantní i proud rezistorem. Z~prvního Kirchhoffova zákona pak víme, že proud rezistorem R3 klesne o~hodnotu proudu dodanou z~pinu RA3, tím klesne také napětí na výstupu měniče a dojde ke ztlumení jasu \acs{led} pásku. Citlivost (nebo také rozsah) změny je definována hodnotou R5, snížením jeho hodnoty lze dosáhnout na výstupu ještě nižšího napětí. Pro hodnotu \(R_{5} = \qty{100}{k\ohm}\) zobrazenou ve schématu lze nejnižší možné napětí vypočítat následovně:
    \begin{equation}
        U_{outMIN} = \num{0.8}+R_{3} \cdot I_{3} = \num{0.8}+R_{3} \cdot \left(\frac{\num{0.8}}{R_{4}} - \frac{U_{VDD} - U_{D1}}{R_{4}+R_{5}} \right) 
    \end{equation}  
    Kdy \(U_{VDD} = \qty{3.3}{V}\) je maximální napětí pinu RA3 a \(U_{D1}=\qty{0.35}{V} \) je prahové napětí zvolené diody. Po dosazení získáme:
    \begin{equation}
        U_{outMIN} = \num{0.8}+\qty{140}{k} \cdot \left(\frac{\num{0.8}}{\qty{10}{k}} - \frac{\num{3.3} - \num{0.35}}{\qty{10}{k}+\qty{100}{k}} \right) = \qty{8.25}{V}
    \end{equation}  
    Toto napětí by mělo být dostatečně nízké k~úplnému zhasnutí \acs{led} pásku.

    Pro zajištění stability obvodu je navržena externí kompenzační síť. Je složena ze tří součástek připojených mezi pin COMP a zem. Tyto sítě se navrhují z~důvodů zlepšení odezvy systému na rychlé změny výstupního proudu. V~ideálním případě chceme, aby systém zareagoval co nejrychleji, ale současně nedošlo k~jeho rozkmitání. Vzhledem ke scénáři, kdy MCU uměle vstupuje do zpětnovazební smyčky, je riskantní pohybovat se na zmíněné hranici. Pro zachování stability byla proto zvolena velmi pomalá odezva systému. Požadoveného zpomalení je dosaženo vysokou hodnota kapacity kompenzačního kondenzátoru, \(C_{4}=\qty{100}{nF} \).

    V~dalším kroku je stanovena hodnota induktoru L1. Výrobce doporučuje zvolit zvlnění proudu induktorem (ripple) \(\Delta I_{L}  \) jako 30 až \qty{50}{\percent} maximálního odběru. Pro výpočet induktoru je uvažován maximální povolený proud čipem, tím je zajištěno, že čip bude fungovat i po překročení maximálního očekávaného proudu \(I_{max} = \qty{1.66}{A} \). Při zvolení střední hodnoty \qty{40}{\percent} získáme:
    \begin{equation}
        \Delta I_{L} = \num{0.4}\cdot I_{IC-max} = \num{0.4} \cdot  \num{3.5} = \qty{1.4}{A}
    \end{equation}
    Odpovídající hodnota indukčnosti je vypočtena následujícím vztahem:
    \begin{equation}
        L_{1} = \frac{U_{outMAX}\cdot (U_{in} -U_{outMAX} ) }{U_{in} \cdot \Delta I_{L}\cdot f_{SW}  }
    \end{equation}
    Po dosazení získáme:
    \begin{equation}
        L_{1} = \frac{12\cdot (24 -12 ) }{24 \cdot \num{1.4}\cdot \qty{450}{k}  } = \qty{9.52}{\micro H}
    \end{equation}
    Zvolíme nejbližší běžně používanou hodnotu \(L_{1} = \qty{10}{\micro H}\). 

    Pro vstupní (C1) a výstupní (C6) kapacitu použijeme hodnoty doporučené výrobcem, stejně tak pro bootstrap kondenzátor C3. 
    
    Poslední součástkou zůstává měřicí rezistor R6. Tímto rezistorem protéká celý výstupní proud měniče, v~rámci minimalizace ztrátového výkonu by měl mít tedy co nejmenší odpor. Musíme ovšem také brát v~potaz rozsah měřicího zesilovače INA180A4. Tato součástka se vyrábí v~několika variantách, byla zvolena varianta s~nejvyšším ziskem \(G_{INA}=200 \) pro zachování co nejnižší hodnoty rezistoru, výstupní napětí zesilovače je v~rozsahu 0 až \qty{3.3}{V} (VDD mikrokontroléru).
    Při maximálním očekávaném proudu chceme dosáhnout horní hranice rozsahu zesilovače, z~této podmínky vyplývá vztah pro výpočet odporu rezirtoru R6:
    \begin{equation}
        R_{6} = \frac{U_{VDD}}{I_{max} \cdot G_{INA} } = \frac{\num{3.3}}{\num{1.66}\cdot 200} = \qty{9.94}{m\ohm}
    \end{equation} 
    Zvolíme blízkou hodnotu \(R_{6} \) = \qty{10}{m\ohm}.

\subsubsection{Očekávané parametry}
    Pro výpočet výstupního zvlnění (v~uzlu I.) chybí údaj o~ekvivalentním sériovém odporu (ESR) výstupních kondenzátorů (C6), který výrobce neuvádí. Vyjdeme tedy z~typické hodnoty pro keramický kondenzátor \(ESR=\qty{15}{m\ohm}\)~\cite{wikipedia2024esr}, kdy počítáme s~paralelní kombinací tří kondenzátorů.
    Očekávané výstupní zvlnění je tedy přibližně:
    \begin{equation}
        \label{rovnice:led_modul}
        \Delta U_{out} = \Delta I_{L} \cdot  \left(\frac{ESR}{3}+\frac{1}{8\cdot f_{SW} \cdot C_{6} }\right) 
    \end{equation} 
    \begin{equation}
        \Delta U_{out} = \num{1.4} \cdot  \left(\frac{\qty{15}{m}}{3}+\frac{1}{8\cdot \qty{450}{k} \cdot 3\cdot \qty{22}{\micro\,} }\right)  = \qty{13}{mV}
    \end{equation} 

    Výpočet výsledné účinnosti synchronního buck měniče je poměrně komplexním problémem~\cite{texasBuckEfficiency}. K~jejímu odhadu je potřeba stanovit hodnotu ztrátového výkonu jednotlivých částí měniče. U~integrovaného řešení, jako je i použitý čip AP63356Q, výrobce často uvádí pouze hodnoty základních parametrů. Chybí detaily zejména o~integrovaných tranzistorech, které jsou klíčové pro výpočet spínacích ztrát. Jako možnost tedy zbývá přibližný odečet z~grafů katalogového listu nebo využití kalkulačky dodané výrobcem~\cite{diodesAP6335xQ}, která v~sobě obsahuje přesnější výpočetní rovnice. 

    Po dosazení odpovídajích hodnot do kalkulačky výrobce je odhadovaná účinnost celého obvodu (při maximálním zatížení jednoho kanálu) \(\eta=\qty{96}{\percent}\) a ztrátový výkon \(P_{Z} = \qty{0.84}{W}\). 

\subsection{Tvorba \acs{dps}}
    Jak již bylo zmíněno v~úvodu kapitoly, jedná se o~dceřinnou desku pro obecný modul periferie, čímž jsou jasně určeny její maximální rozměry. Stejně jako u~předešlých návrhů, i zde je použita čtyřvrstvá struktura viz obr.~\ref{fig:ridici-jednotka-stackup-dps}. Vizualizace návrhu se nachází na obr.~\ref{fig:perif-led-dps} spolu s~ukázkou sesazení s~obecným modulem periferie. 

    \begin{figure}[!ht]
        \centering
        \begin{tikzpicture}
            % Include the image
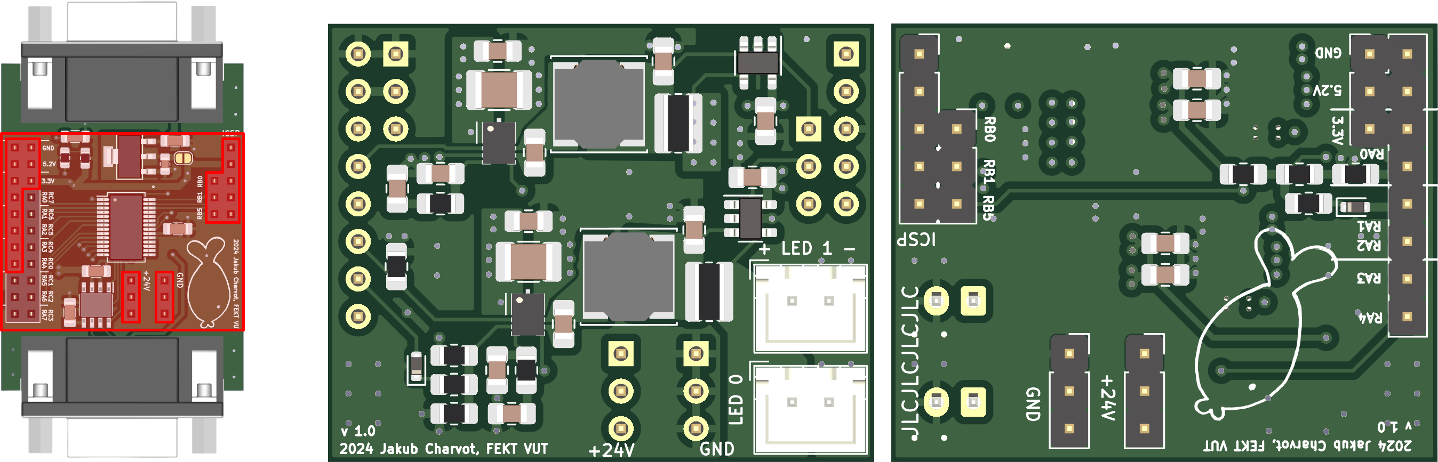
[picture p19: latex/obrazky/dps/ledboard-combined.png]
            \node[anchor=south west,inner sep=0] (image) at (0,0) {};
            
            \draw[dashed] (10.1,0.02) -- (12.5,0.02);
            \draw[<->,thick] (12.5,0.02) -- (12.5,3.66);
            \draw[dashed] (12.5,3.66) -- (10.1,3.66);
            \node[anchor=west] at (12.5,1.83)  {\qty{36}{mm}};

            \draw[dashed] (2.75,0.02) -- (2.75,-0.5);
            \draw[<->,thick] (2.75,-0.6) -- (7.3,-0.6);
            \draw[dashed] (7.3,-0.6) -- (7.3,0.02);
            \node[anchor=south] at (5,-0.6)  {\qty{57}{mm}};

            \draw[dashed,thick,color=red] (2.75,0.02) -- (2.05,1.1);
            \draw[dashed,thick,color=red] (2.75,3.66) -- (2.05,2.7);
        \end{tikzpicture}
        \caption{Vizualizace \acs{dps} periferie \acs{led} osvětlení.}
        \label{fig:perif-led-dps}
    \end{figure}

    Za účelem zvětšení plochy pro umístění součástek byly z~konektorů obecného modulu vyvedeny pouze některé piny, i přesto bylo nakonec potřeba umístit komponenty také na spodní stranu \acs{dps}. Rozmístění součástek je obdobné pro oba měniče napětí a respektuje doporučení výrobce a tedy i obecná pravidla pro návrh měničů napětí~\cite{Diodes_AP63356Q}. Je kladen důraz na to, aby smyčka ze spínacího uzlu přes výstupní kapacitu a zem zpět do kontroléru byla co nejkratší a vedena za pomoci polygonů. Stejně tak vstupní kapacitor je umístěn přímo vedle vstupních pinů kontroléru.

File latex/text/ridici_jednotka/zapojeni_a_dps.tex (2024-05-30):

\section{Návrh zapojení a tvorba \acs{dps}}
\label{sec:ridici-jednotka-schema-a-dps}
    Řídicí jednotka je tvořena jednou \acs{dps}, která kromě samotného mikrokontroléru obsahuje také měnič napětí typu buck ke snížení napájecího napětí externího zdroje na hodnotu \qty{5.2}{V}. Toto napětí je pak dále používáno pro napájení samotného mikrokontroléru řídicí jednotky a zároveň je vyvedeno na konektor pro připojení periferií. Blokové schéma na úrovni logických bloků v~rámci jedné \acs{dps} je na obr.~\ref{fig:ridici-jednotka-blokove-schema}, jednotlivým částem se blíže věnují další kapitoly. Celé schéma je k~dispozici v~příloze~\ref{priloha:schema-a-dps-ridici-jednotka}.

    % Blokove schema
    \begin{figure}[h!]
        \centering
        \begin{tikzpicture}[
            module/.style={%
        draw, rounded corners,
        minimum width=#1,
        minimum height=7mm,
        font=\sffamily,
        align=center
        },
    module/.default=2cm,
    >=LaTeX]
        
            % ridici
            \node[module] (mcu) {MCU};
            \node[module, left=of mcu] (ldo) {LDO}; 
            \node[module, above=of ldo] (buck) {DC/DC měnič};
            \node[module, right=of mcu] (candriver) {\acs{can} řadič};
            \node[module, above right=10mm and -5mm of candriver] (konperif) {Konektory periferií};
            \node[module, above=of buck] (24v) {Externí modul\\Zdroj \qty{24}{V}};
            \node[module, below=of mcu] (konektory) {Konektory};
            \node[module=1cm, below right=9mm and -7mm of konektory] (konektor1) {Stavové \acs{led}};
            \node[module=1cm, below left= 9mm and -8mm of konektory] (konektor2) {Displej};
            \node[module=1cm, below right= 0mm and 6mm of konektory] (konektor3) {Relé};
            \node[module=1cm, below left= 0mm and 6mm of konektory] (konektor4) {Rozšíření};

            \node[fit=(konektor1) (konektor2) (konektor3) (konektor4) (buck) (konperif) (mcu), draw, inner sep=2mm] (fitridici) {};
            % Connections
            \foreach \i in {1,2,3}
                \draw[->] (konektory)--(konektor\i);
            \draw[<->] (konektory)--(konektor4);
            \draw[<->] (konektory)--(mcu);
            \draw[->] (buck)--(ldo);
            \draw[->] (ldo)--(mcu);
            \draw[<->] (candriver)--(mcu);
            \draw[->] (buck)--(konperif);
            \draw[<->] (candriver)--(konperif);

            \draw[->,dashed] (24v) to [out=0,in=115] (konperif);
            \draw[->,dashed] (24v)--(buck);
        
        \end{tikzpicture}
        
        \caption{Blokové schéma řídicí jednotky.}
        \label{fig:ridici-jednotka-blokove-schema}
    \end{figure}

    \subsection{Zapojení ESP32 modulu}
    \label{sec:ridici-jendotka-esp32-modul}
        Při tvorbě schématu bylo vycházeno z~dokumentace výrobce~\cite{esp32-wroom-32e-datasheet} a také ze schémat různých existujících vývojových desek. K~zajištění správné a spolehlivé funkce modulu je potřeba dodržet několik věcí. Výřez schématu obsahující potřebné doplňující obvody pro ESP32 modul je na obr.~\ref{fig:ridici-jednotka-esp-obvody}.

        \begin{figure}[h!]
            \centering
            % trim=left bottom right top
            \includegraphics
            [
                width=0.9\textwidth, 
                page=2, 
                trim=2.5cm 8.5cm 15.5cm 2cm, 
                clip
            ]{obrazky/exportovane/main-board-schematic.pdf}
            \caption{Podpůrné obvody pro modul ESP32-WROOM-E. Vytvořeno v~KiCad 7.0.}
            \label{fig:ridici-jednotka-esp-obvody}
        \end{figure}

        Na napájecí pin (3V3) je třeba přivést stabilní napětí a opatřit ho blokovacími kondenzátory (C3, C4). Ke snížení napětí z~původních \qty{5,2}{V} na požadovaných \qty{3,3}{V} je použit lineární regulátor TLV76133 (U2).
        
        % TODO: Čas ke stabilizaci bude mnohem větší než 50 us. Nejprve totiž musí naběhnout 3V3, což trvá dle datasheetu TLV76133 trvá cca 500 us. Taky bys správně měl zohlednit i náběh 5V2, což je 3 ms.
        Dále je potřeba přivést kladné napětí na povolovací pin (EN). Z~dokumentace vyplývá, že by mělo být přivedeno až po ustálení napájecí linky. Uvedený čas nutný ke stabilizaci je roven \(t_{STBL}=\qty{50}{\micro\second}\)~\cite{esp32-datasheet}. Požadované zpoždění zajistí RC článek (R1, C5) s~časovou konstantou \(\tau\):
        \begin{equation}
            \tau=R_{1}C_{5}=\qty{10}{\kilo\ohm}\cdot \qty{1}{\micro\farad}=\qty{10}{\milli\second}
        \end{equation} 
        Jak je vidět, byla zvolena dostatečná návrhová rezerva. 

        Pro možnost resetu zařízení a vstupu do bootloaderu byla doplněna také dvě tlačítka (SW1, SW2).

    \subsection{Napájecí obvod}
        \label{sec:ridici-jendotka-napajeci-obvod}
        Pro napájení celého zařízení je použit externí zdroj stejnosměrného napětí \qty{24}{V} a toto napětí je také rozvedeno všem připojeným periferiím. Pro většinu komponent je ale nutné napětí snížit. K~tomuto účelu byl navržen DC/DC měnič typu buck s~požadovaným výstupním napětím \qty{5.2}{V}. Existuje celá řada čipů vyvinutých pro tento účel. Aplikace v~tomto zařízení je specifická svými požadavky na výstupní proud. Zatímco samotná řídicí jednotka nebude odebírat velký proud, není jasně dané, kolik periferí a s~jakými výkonovými požadavky uživatel k~systému připojí. Navržený měnič tak musí fungovat v~širším rozsahu proudů (řádově od desítek mA po jednotky A), a to s~co nejlepší účinností. 
        
        \begin{figure}[h!]
            \centering
            % trim=left bottom right top
            \includegraphics
            [
                width=\textwidth, 
                page=2, 
                trim=2.2cm 8.5cm 13cm 1.3cm, 
                clip
            ]{obrazky/exportovane/ukazky-do-textu.pdf}
            \caption{Napájecí obvod řídicí jednotky. Vytvořeno v~KiCad 7.0.}
            \label{fig:ridici-jednotka-napajeni-simp}
        \end{figure}

        Aby bylo vyhověno zmíněným požadavkům a zachována návrhová rezerva, byl jako základ buck měniče zvolen čip LM5148~\cite{lm5148-datasheet}. Jedná se o~moderní součástku firmy Texas Instruments s~velkou výkonovou rezervou. Tento čip funguje pouze jako buck kontrolér a zapojení je potřeba doplnit dvěma externími MOSFET tranzistory. Většina tepelných ztrát vzniká právě na nich, čímž se sníží ohřev samotného čipu a generované teplo se lépe rozloží. Na volbě tranzistorů závisí také výsledná účinnost měniče. Při návrhu zapojení této součástky byl použit nástroj Webench Power Designer~\cite{webench-power-designer}, který podle zadaných parametrů navrhne konkrétní schéma zapojení, provede simulaci a zobrazí grafy upravené na míru zadaným hodnotám. Tento nástroj uvádí přibližnou účinnost zapojení jako \qty{88}{\percent}. V~navrženém schématu bylo posléze provedeno několik změn, aby vše odpovídalo požadavkům uvedeným v~katalogovém listu součástky~\cite{lm5148-datasheet}. Kompletní schéma zapojení spolu s~odkazy k~relevantním kapitolám katalogového listu se nachází v~příloze~\ref{priloha:schema-ridici-jednotka-napajeci-obvod}, pro přibližnou představu pak postačí zjednodušené schéma na obr.~\ref{fig:ridici-jednotka-napajeni-simp}. 

        \subsubsection{Hodnoty součástek}
        Označení součástek používané v~této kapitole je vztaženo ke zjednodušenému schématu na obr.~\ref{fig:ridici-jednotka-napajeni-simp}. Součástky okolo čipu LM5148 lze rozdělit na dvě skupiny. V~prvé řadě ty součástky, které spolu s~čipem tvoří jádro buck měniče. Jsou jimi externí tranzistory Q1 (high-side) a Q2 (low-side), induktor L2, vstupní kapacitory (C7,C8) a výstupní kapacitory (C13). Také sem lze zaředit snímací rezistor R13. Pro tyto součástky byly použity hodnoty doporučené výrobcem v~katalogovém listu pro danou aplikaci~\cite{lm5148-datasheet}. Druhou skupinu tvoří součástky nutné ke správnému nastavení buck kontroléru. Jejich možné hodnoty pro různá nastavení jsou opět specifikovány v~katalogovém listu. 

        Rezistor R12 slouží k~nastavení frekvence spínání, ze zvolené hodnoty vyplývá frekvence:
        \begin{equation}
            f_{SW}[\unit{kHz}] = \frac{\num{10e6}}{45\cdot R_{12}[\unit{k\ohm}]+53 }
        \end{equation}
        \begin{equation}
            f_{SW} = \frac{\num{10e6}}{45\cdot \num{35.7}+53 } = \qty{602.59}{kHz}
        \end{equation}

        Výstupní napětí je dáno poměrem odporového děliče R9 a R10. Na pinu FB je udržováno konstantní napětí \(U_{FB} = \qty{0.8}{V}\), z~této podmínky pak vyplývá vztah pro výstpní napětí:
        \begin{equation}
            U_{OUT}  = U_{FB}\cdot \frac{R_{9} +R_{10}}{R_{10}}
        \end{equation}
        \begin{equation}
            U_{OUT}  = \num{0.8}\cdot \frac{\num{54.9e3} +\num{10e3}}{\num{10e3}} = \qty{5.192}{V}
        \end{equation}

        Připojením pull-up rezistoru R8 mezi piny EXTCOMP a VDDA dojde k~nastavení interní kompenzace, která je v~tuto chvíli dostatečná a není potřeba tvořit kompenzační síť. Pro jistotu byl ale na výsledné DPS vyhrazen prostor i pro součástky kompenzační sítě, viz úplné schéma v~příloze~\ref{priloha:schema-ridici-jednotka-napajeci-obvod}. 

        Čip LM5148 nabízí možnost pracovat paralelně v~synchronizaci s~druhým stejným čipem. Tato funkce zde nebude potřeba, tak stačí synchronizační pin PG/SYNCOUT pull-up rezistorem R11 spojit s~napětím VCC, tím se přepne do módu indikátoru správnosti výstupního napětí (PG = Power Good). 

        Poslední důležitou součástkou je rezistor R7 sloužící pro zbylá nastavení. Hodnota \(R_{7} = \qty{41.2}{k\ohm}\) indikuje nastavení módu primárního kontroléru (viz předešlý odstavec). Dále zapříčiňuje vypnutí módu Dual Phase a zapnutí použití rozprostřeného spektra (Spread spectrum).

    \subsection{Deska plošných spojů}
        Ačkoliv se jedná o~relativně jednoduchou \acs{dps}, je potřeba při návrhu dbát jistých pravidel a doporučení. Modul ESP32 je vybaven anténou a volba jeho umístění na \acs{dps} je rozhodujícím faktorem pro správnou funkci antény. Další částí vyžadující optimální návrh rozložení a propojení součástek je pak buck měnič. 
        
        \begin{figure}[!ht]
            \centering
            \begin{tikzpicture}
                % Include the image
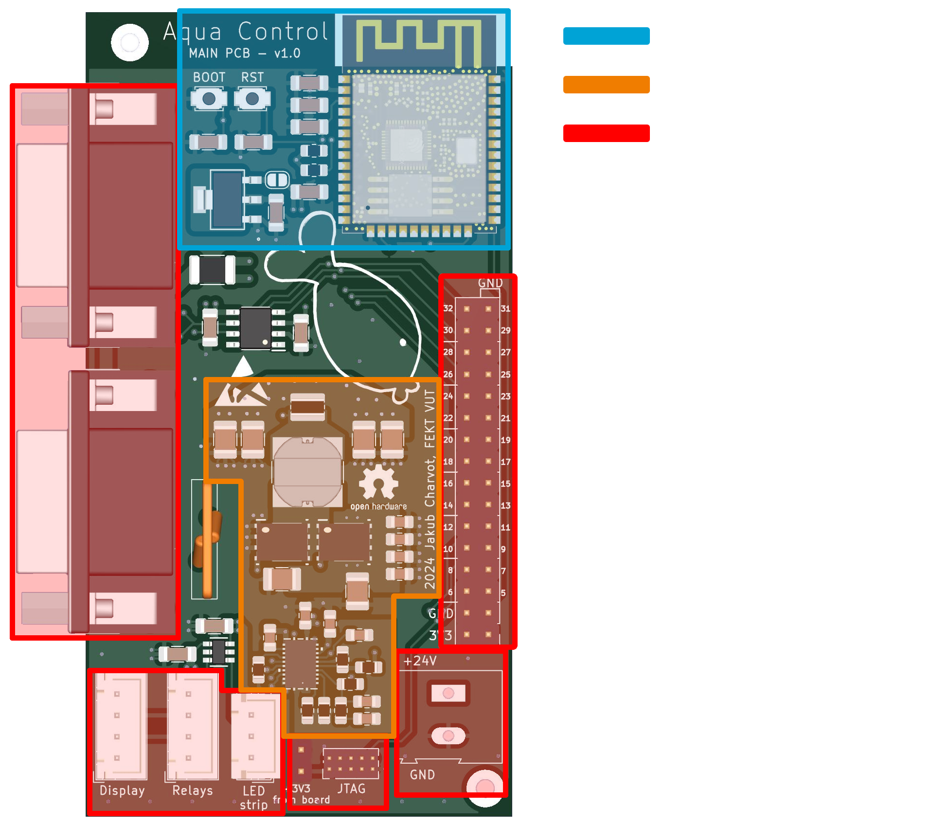
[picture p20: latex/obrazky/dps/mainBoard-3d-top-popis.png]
                \node[anchor=south west,inner sep=0] (image) at (0,0) {};
                
                % \draw[->,thick] (0,0) -- (1,9.4);
                \node[anchor=south west,inner sep=0,color=red] at (0.5,9.7)  {1.};
                \node[anchor=south west,inner sep=0,color=red] at (0.6,1.3)  {2.};
                \node[anchor=south west,inner sep=0,color=red] at (4.2,-0.4)  {3.};
                \node[anchor=south west,inner sep=0,color=red] at (6.8,1.3)  {4.};
                \node[anchor=south west,inner sep=0,color=red] at (6.8,5)  {5.};
                % legend
                \node[anchor=south west,inner sep=0] (leg-blu) at (8.5,10)  {\acs{mcu}};
                \node[anchor=south west,inner sep=0] (leg-ora) at (8.5,9.32) {buck měnič napětí};
                \node[anchor=south west,inner sep=0] (leg-red) at (8.5,8.64) {Konektory:};

                \node[below left=0.8 and 0.6 of leg-red, anchor=south west] (kon1) {1. Ovládané periferie};
                \node[below left=0.6 and 0.0 of kon1, anchor=south west] (kon2) {2. Externí moduly};
                \node[below left=0.6 and 0.0 of kon2, anchor=south west] (kon3) {3. Programování};
                \node[below left=0.6 and 0.0 of kon3, anchor=south west] (kon4) {4. Vstup napájení};
                \node[below left=0.6 and 0.0 of kon4, anchor=south west] (kon5) {5. Testování, rozšíření};
                % \node[anchor=south west,inner sep=0,color=red] {2.};
                % \node[anchor=south west,inner sep=0,color=red] {3.};
                % \node[anchor=south west,inner sep=0,color=red] {4.};
                % \node[anchor=south west,inner sep=0,color=red]          {5.};
            \end{tikzpicture}
            \caption{Vizualizace \acs{dps} řídicí jednotky s~vyznačením jednotlivých částí.}
            \label{fig:ridici-jednotka-dps-popis}
        \end{figure}

        Prvním krokem návrhu je volba počtu vrstev a jejich funkce. Vyšší počet vrstev nabízí více prostoru pro vedení cest a také umožňuje vedení napájecích napětí pomocí rozlitých měděných polygonů, čímž se zároveň zlepší vlastnosti zařízení z~hlediska \acs{emc}. Zvolený výrobce (JLC PCB~\cite{jlcpcb}) nabízí výrobu desek s~jednou až dvaceti vrstvami mědi. Byla zvolena čtyřvrstvá deska, která je pro danou aplikaci dostatečná a stále se nachází v~přijatelné cenové skupině výrobce. Rozložení a funkce vrstev jsou vyobrazeny na obr.~\ref{fig:ridici-jednotka-stackup-dps}.
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

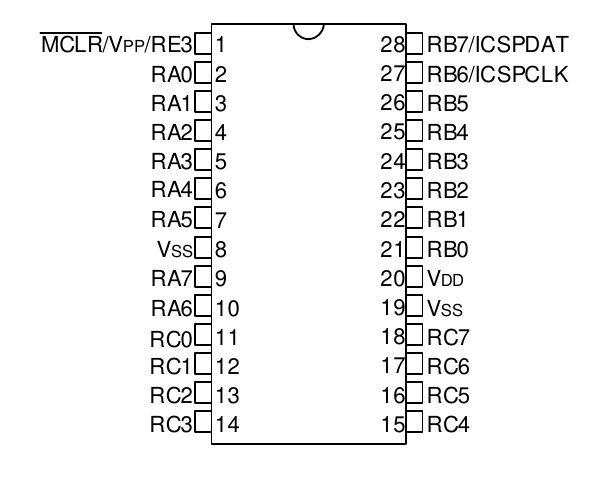
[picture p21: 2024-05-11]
sw/docs/PICpinout.png

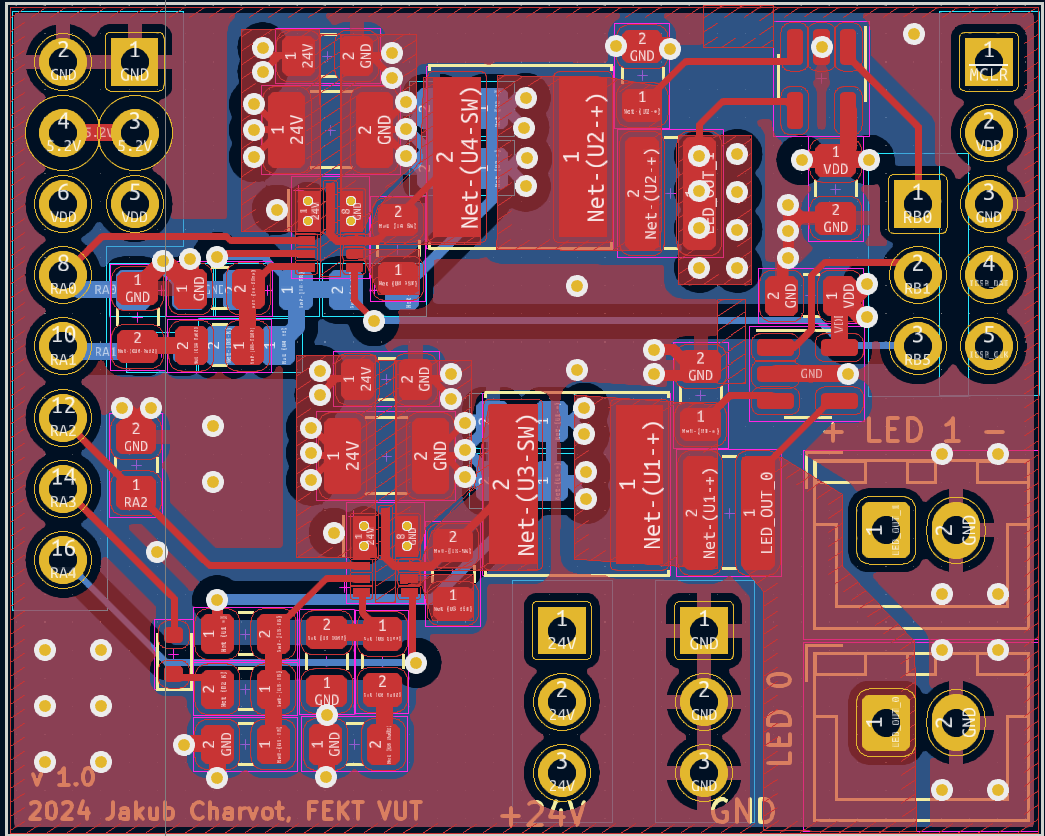
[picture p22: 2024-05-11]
sw/docs/leddps.png

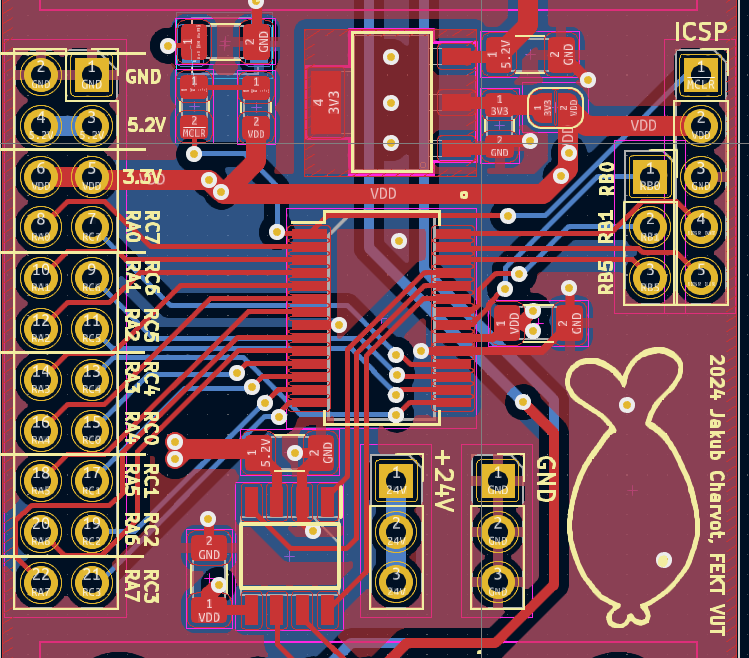
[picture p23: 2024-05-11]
sw/docs/dps.png

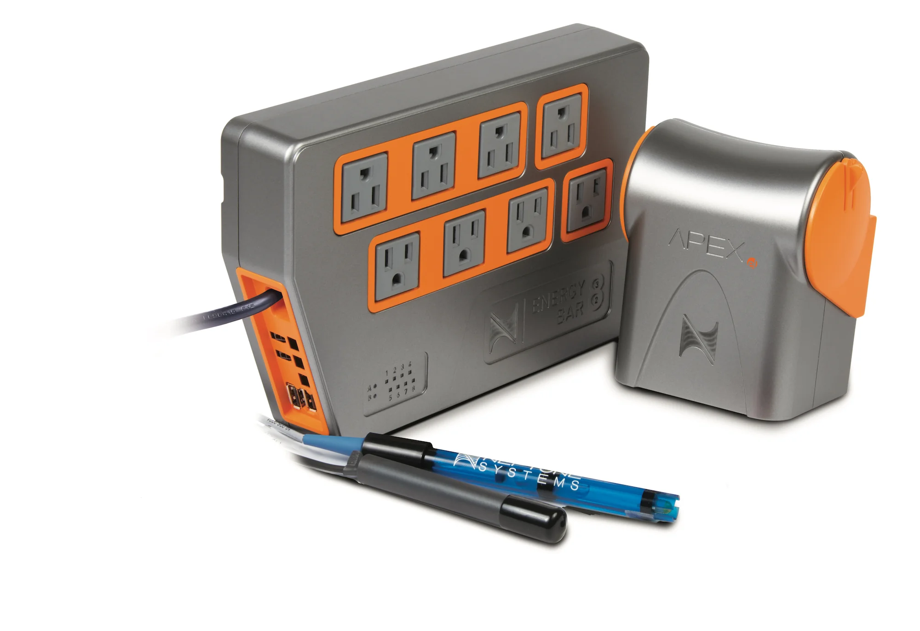
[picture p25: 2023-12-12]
latex/obrazky/trh/apex-el.webp

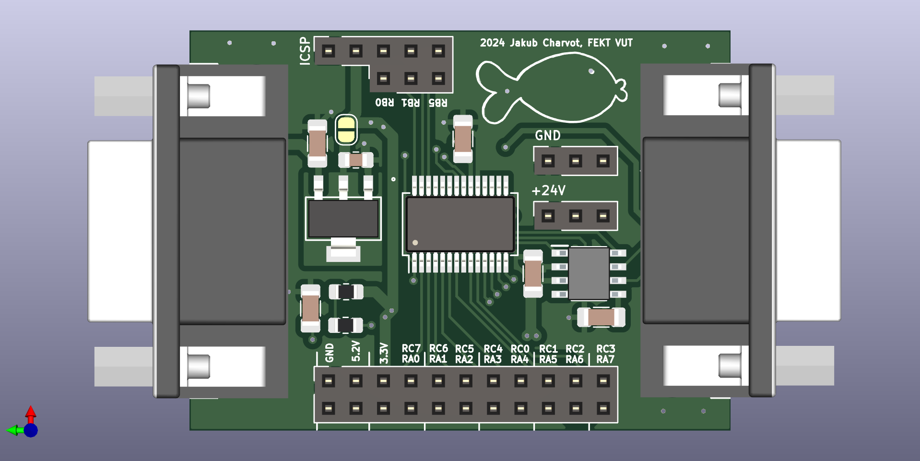
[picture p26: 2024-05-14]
latex/obrazky/dps/peripherial-module-3d/peripherialModule3d.png

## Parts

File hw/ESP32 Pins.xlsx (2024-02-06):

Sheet: WROOM
No. | Name | Type | GPIO | True GPIO | RTC_GPIO | ADC | TOUCH | DAC | I2C | SPI | SD/SDIO/MMC Host Controller | UART | Parallel QSPI | JTAG | SDIO Slave | Ethernet | SD/SDIO/MMC Host Controller |  | Value on boot time | My usage
25 | IO00 | I/O | GPIO00 | No | RTC_GPIO11 | ADC2_CH01 | TOUCH1 |  |  |  |  |  |  |  |  | EMAC_TX_CLK |  | Low for programming | HIGH | -
35 | TXD0 | I/O | GPIO01 | No |  |  |  |  |  |  |  | U0TXD |  |  |  | EMAC_RXD2 |  |  |  | U0TXD
24 | IO02 | I/O | GPIO02 | No | RTC_GPIO12 | ADC2_CH02 | TOUCH2 |  |  |  | HS2_DATA0 |  | HSPIWP |  |  |  | HS2_DATA0 | floarting or low for flashing | LOW | -
34 | RXD0 | I/O | GPIO03 | No |  |  |  |  |  |  |  | U0RXD |  |  |  |  |  |  |  | U0RXD
26 | IO04 | I/O | GPIO04 |  | RTC_GPIO10 | ADC2_CH0 | TOUCH0 |  |  |  | HS2_DATA1 |  | HSPIHD |  |  | EMAC_TX_ER | HS2_DATA1
29 | IO05 | I/O | GPIO05 |  |  |  |  |  |  | SS/CS |  |  | VSPICS0 |  |  | EMAC_RX_CLK | HS1_DATA6 |  | HIGH | -
20 | SCK/CLK* | I/O | GPIO06 | No | UNUSABLE !!! (Flash memory) |  |  |  |  |  |  | U1CTS | SPICLK |  | SD_CLK |  | HS1_CLK |  |  | -
21 | SDO/SD0* | I/O | GPIO07 | No | UNUSABLE !!! (Flash memory) |  |  |  |  |  |  | U2RTS | SPIQ |  | SD_DATA0 |  | HS1_DATA0 |  |  | -
22 | SDI/SD1* | I/O | GPIO08 | No | UNUSABLE !!! (Flash memory) |  |  |  |  |  |  | U2CTS | SPID |  | SD_DATA1 |  | HS1_DATA1 |  |  | -
17 | SHD/SD2* | I/O | GPIO09 | No | UNUSABLE !!! (Flash memory) |  |  |  |  |  |  | U1RXD | SPIHD |  | SD_DATA2 |  | HS1_DATA2 |  |  | -
18 | SWP/SD3* | I/O | GPIO10 | No | UNUSABLE !!! (Flash memory) |  |  |  |  |  |  | U1TXD | SPIWP |  | SD_DATA3 |  | HS1_DATA3 |  |  | -
19 | SCS/CMD* | I/O | GPIO11 | No | UNUSABLE !!! (Flash memory) |  |  |  |  |  |  | U1RTS | SPICS0 |  |  |  | HS1_CMD |  |  | -
14 | IO12 | I/O | GPIO12 | No | RTC_GPIO15 | ADC2_CH05 | TOUCH5 |  |  |  | HS2_DATA2 |  | HSPIQ | MTDI |  | EMAC_TXD3 | HS2_DATA2 | Must not be high during boot! | LOW | MTDI
16 | IO13 | I/O | GPIO13 |  | RTC_GPIO14 | ADC2_CH04 | TOUCH4 |  |  |  | HS2_DATA3 |  | HSPID | MTCK |  | EMAC_RX_ER | HS2_DATA3 |  |  | MTCK
13 | IO14 | I/O | GPIO14 |  | RTC_GPIO16 | ADC2_CH06 | TOUCH6 |  |  |  | HS2_CLK |  | HSPICLK | MTMS |  | EMAC_TXD2 | HS2_CLK |  |  | MTMS
23 | IO15 | I/O | GPIO15 |  | RTC_GPIO13 | ADC2_CH03 | TOUCH3 |  |  |  | HS2_CMD |  | HSPICS0 | MTDO |  | EMAC_RXD3 | HS2_CMD | Prevents startup log | HIGH | MTDO
27 | IO16 | I/O | GPIO16 | Not available on WROVER |  |  |  |  |  |  |  | U2RXD |  |  |  | EMAC_CLK_OUT | HS1_DATA4 | PSRAM for the WROVER
28 | IO17 | I/O | GPIO17 | Not available on WROVER |  |  |  |  |  |  |  | U2TXD |  |  |  | EMAC_CLK_OUT_180 | HS1_DATA5 | PSRAM for the WROVER |  | LED_STRIP
30 | IO18 | I/O | GPIO18 |  |  |  |  |  |  | SCLK |  |  | VSPICLK |  |  |  | HS1_DATA7 |  |  | pull up
31 | IO19 | I/O | GPIO19 |  |  |  |  |  |  | MISO |  | U0CTS | VSPIQ |  |  | EMAC_TXD0
33 | IO21 | I/O | GPIO21 |  |  |  |  |  | SDA1 |  |  |  | VSPIHD |  |  | EMAC_TX_EN |  |  |  | SDA1
36 | IO22 | I/O | GPIO22 |  |  |  |  |  | SCL1 |  |  | U0RTS | VSPIWP |  |  | EMAC_TXD1 |  |  |  | SCL1
37 | IO23 | I/O | GPIO23 |  |  |  |  |  |  | MOSI |  |  | VSPID |  |  |  | HS1_STROBE
10 | IO25 | I/O | GPIO25 |  | RTC_GPIO06 | ADC2_CH08 |  | DAC_1 |  |  |  |  |  |  |  | EMAC_RXD0 |  |  |  | CAN_STBY
11 | IO26 | I/O | GPIO26 |  | RTC_GPIO07 | ADC2_CH09 |  | DAC_2 |  |  |  |  |  |  |  | EMAC_RXD1 |  |  |  | CAN_RX
12 | IO27 | I/O | GPIO27 |  | RTC_GPIO17 | ADC2_CH07 | TOUCH7 |  |  |  |  |  |  |  |  | EMAC_RX_DV |  |  |  | CAN_TX
8 | IO32 | I/O | GPIO32 |  | RTC_GPIO09 | ADC1_CH04 | TOUCH9 |  |  |  |  |  |  |  |  |  |  | XTAL_32K_P (32.768kHz crystal oscillator input)
9 | IO33 | I/O | GPIO33 |  | RTC_GPIO08 | ADC1_CH05 | TOUCH8 |  |  |  |  |  |  |  |  |  |  | XTAL_32K_N (32.768kHz crystal oscillator outut)
6 | IO34 | I | GPIO34 | No | RTC_GPIO04 | ADC1_CH06 |  |  |  |  |  |  |  |  |  |  |  | No internal pullup |  | -
7 | IO35 | I | GPIO35 | No | RTC_GPIO05 | ADC1_CH07 |  |  |  |  |  |  |  |  |  |  |  | No internal pullup |  | -
4 | SENSOR_VP | I | GPIO36 | No | RTC_GPIO00 | ADC1_CH0 |  |  |  |  |  |  |  |  |  |  |  | No internal pullup |  | -
5 | SENSOR_VN | I | GPIO39 | No | RTC_GPIO03 | ADC1_CH03 |  |  |  |  |  |  |  |  |  |  |  | No internal pullup |  | -

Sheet: ESP32 Chip
Name | No. | Type |  |  |  |  |  |  |  |  | Function
VDDA | 1 | P | Analog power supply (2.3V ~ 3.6V)
LNA_IN | 2 | I/O | RF input and output
VDD3P3 | 3 | P | Power supply (2.3V ~ 3.6V)
VDD3P3 | 4 | P | Power supply (2.3V ~ 3.6V)
SENSOR_VP | 5 | I | GPIO36 | ADC_PRE_AMP | ADC1_CH0 |  |  |  |  |  | RTC_GPIO0 Note: Connects a 270 pF capacitor from SENSOR_VP to SENSOR_ CAPP w
SENSOR_CAPP | 6 | I | GPIO37 | ADC_PRE_AMP | ADC1_CH1 |  |  |  |  |  | RTC_GPIO1 Note: Connects a 270 pF capacitor from SENSOR_VP to SENSOR_ CAPP w
SENSOR_CAPN | 7 | I | GPIO38 | ADC1_CH2 | ADC_PRE_AMP |  |  |  |  |  | RTC_GPIO2 Note: Connects a 270 pF capacitor from SENSOR_VN to SENSOR_ CAPN w
SENSOR_VN | 8 | I | GPIO39 | ADC1_CH3 | ADC_PRE_AMP |  |  |  |  |  | RTC_GPIO3 Note: Connects a 270 pF capacitor from SENSOR_VN to SENSOR_ CAPN w
CHIP_PU | 9 | I | High: On; enables the chip Low: Off; resets the chip Note: Do not leave the CHIP_PU pin floating.
VDET_1 | 10 | I | GPIO34 | ADC1_CH6 |  |  |  |  |  |  | RTC_GPIO4
VDET_2 | 11 | I | GPIO35 | ADC1_CH7 |  |  |  |  |  |  | RTC_GPIO5
32K_XP | 12 | I/O | GPIO32 | ADC1_CH4 | 32K_XP (32.768 kHz crystal oscillator input) | TOUCH9 |  |  |  |  | RTC_GPIO9
32K_XN | 13 | I/O | GPIO33 | ADC1_CH5 | 32K_XN (32.768 kHz crystal oscillator output) | TOUCH8 |  |  |  |  | RTC_GPIO8
GPIO25 | 14 | I/O | GPIO25 | ADC2_CH8 | DAC_1 | RTC_GPIO6 |  |  |  |  | EMAC_RXD0
GPIO26 | 15 | I/O | GPIO26 | ADC2_CH9 | DAC_2 | RTC_GPIO7 |  |  |  |  | EMAC_RXD1
GPIO27 | 16 | I/O | GPIO27 | ADC2_CH7 | TOUCH7 | RTC_GPIO17 |  |  |  |  | EMAC_RX_DV
MTMS | 17 | I/O | GPIO14 | ADC2_CH6 | TOUCH6 | RTC_GPIO16 | MTMS | HSPICLK | HS2_CLK | SD_CLK | EMAC_TXD2
MTDI | 18 | I/O | GPIO12 | ADC2_CH5 | TOUCH5 | RTC_GPIO15 | MTDI | HSPIQ | HS2_DATA2 | SD_DATA2 | EMAC_TXD3
VDD3P3_RTC | 19 | P | Input power supply for RTC IO (1.8V ~ 3.6V)
MTCK | 20 | I/O | GPIO13 | ADC2_CH4 | TOUCH4 | RTC_GPIO14 | MTCK | HSPID | HS2_DATA3 | SD_DATA3 | EMAC_RX_ER
MTDO | 21 | I/O | GPIO15 | ADC2_CH3 | TOUCH3 | RTC_GPIO13 | MTDO | HSPICS0 | HS2_CMD | SD_CMD | EMAC_RXD3
GPIO2 | 22 | I/O | GPIO2 | ADC2_CH2 | TOUCH2 | RTC_GPIO12 | HSPIWP | HS2_DATA0 |  |  | SD_DATA0
GPIO0 | 23 | I/O | GPIO0 | ADC2_CH1 | TOUCH1 | RTC_GPIO11 | CLK_OUT1
GPIO4 | 24 | I/O | GPIO4 | ADC2_CH0 | TOUCH0 | RTC_GPIO10 | HSPIHD | HS2_DATA1 | SD_DATA1 |  | EMAC_TX_ER
GPIO16 | 25 | I/O | GPIO16 | HS1_DATA4 | U2RXD |  |  |  |  |  | EMAC_CLK_OUT
VDD_SDIO | 26 | P | Output power supply: 1.8V or the same voltage as
GPIO17 | 27 | I/O | GPIO17 | HS1_DATA5 | U2TXD |  |  |  |  |  | EMAC_CLK_OUT_180
SD_DATA_2 | 28 | I/O | GPIO9 | SD_DATA2 | SPIHD | HS1_DATA2 | UNUSABLE !!! (Flash memory) |  |  |  | U1RXD
SD_DATA_3 | 29 | I/O | GPIO10 | SD_DATA3 | SPIWP | HS1_DATA3 | UNUSABLE !!! (Flash memory) |  |  |  | U1TXD
SD_CMD | 30 | I/O | GPIO11 | SD_CMD | SPICS0 | HS1_CMD | UNUSABLE !!! (Flash memory) |  |  |  | U1RTS
SD_CLK | 31 | I/O | GPIO6 | SD_CLK | SPICLK | HS1_CLK | UNUSABLE !!! (Flash memory) |  |  |  | U1CTS
SD_DATA_0 | 32 | I/O | GPIO7 | SD_DATA0 | SPIQ | HS1_DATA0 | UNUSABLE !!! (Flash memory) |  |  |  | U2RTS
SD_DATA_1 | 33 | I/O | GPIO8 | SD_DATA1 | SPID | HS1_DATA1 | UNUSABLE !!! (Flash memory) |  |  |  | U2CTS
GPIO5 | 34 | I/O | GPIO5 | VSPICS0 | HS1_DATA6 |  |  |  |  |  | EMAC_RX_CLK
GPIO18 | 35 | I/O | GPIO18 | VSPICLK |  |  |  |  |  |  | HS1_DATA7
GPIO23 | 36 | I/O | GPIO23 | VSPID |  |  |  |  |  |  | HS1_STROBE
VDD3P3_CPU | 37 | P | Input power supply for CPU IO (1.8V ~ 3.6V)
GPIO19 | 38 | I/O | GPIO19 | VSPIQ | U0CTS |  |  |  |  |  | EMAC_TXD0
GPIO22 | 39 | I/O | GPIO22 | VSPIWP | U0RTS |  |  |  |  |  | EMAC_TXD1
U0RXD | 40 | I/O | GPIO3 | U0RXD |  |  |  |  |  |  | CLK_OUT2
U0TXD | 41 | I/O | GPIO1 | U0TXD | CLK_OUT3 |  |  |  |  |  | EMAC_RXD2
GPIO21 | 42 | I/O | GPIO21 | VSPIHD |  |  |  |  |  |  | EMAC_TX_EN
VDDA | 43 | P | Analog power supply (2.3V ~ 3.6V)
XTAL_N | 44 | O | External crystal output
XTAL_P | 45 | I | External crystal input
VDDA | 46 | P | Digital power supply for PLL (2.3V ~ 3.6V)
CAP2 | 47 | I | Connects to a 3 nF capacitor and 20 kÎ© resistor in parallel
CAP1 | 48 | I | Connects to a 10 nF series capacitor to ground
GND | 49 | P | Ground

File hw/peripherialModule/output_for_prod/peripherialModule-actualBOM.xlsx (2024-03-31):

Typ | Osazeno | Mouser nbr. | Qty. | Id | Designator | Footprint | Quantity | Designation | Supplier and ref
SMD | n | 2 | 100 | 4 | C1,C6,C4,C2 | C_1206_3216Metric_Pad1.33x1.80mm_HandSolder | 4 | 0.10uF
SMD | n | 5 | 20 | 8 | C3 | C_1206_3216Metric_Pad1.33x1.80mm_HandSolder | 1 | 22uF
SMD | n | 8 | 20 | 10 | C5 | C_0805_2012Metric_Pad1.18x1.45mm_HandSolder | 1 | 4.70uF
SMD | n | 16 | 100 | 6 | R1 | R_0805_2012Metric_Pad1.20x1.40mm_HandSolder | 1 | 10k
SMD | n | 26 | 10 | 5 | IC1 | SOIC127P600X175-8N | 1 | ATA6561-GAQW-N
SMD | n | 29 | 10 | 14 | SW1 | SW_SPST_B3U-1000P | 1 | SW_Push
SMD | n | 32? | 2+cz | 1 | U1 | SOT_8DCYR_TEX | 1 | TLV76133DCYR
SMD | n | bastlirna |  | 12 | R2 | R_0805_2012Metric_Pad1.20x1.40mm_HandSolder | 1 | 1k
THT | n | dsub | 26 | 3 | J3,J4 | G17C0900132EU | 2 | G17C0900132EU
SMD | n | ESD sáček |  | 7 | U2 | SSOP-28_5.3x10.2mm_P0.65mm | 1 | PIC18F26Q83
THT | n | x |  | 2 | J1 | PinSocket_2x11_P2.54mm_Vertical | 1 | Conn_02x11_Socket
THT | n | x |  | 9 | J8 | PinSocket_1x05_P2.54mm_Vertical | 1 | Conn_01x05_Socket
THT | n | x |  | 11 | J9,J6,J5 | PinSocket_1x03_P2.54mm_Vertical | 3 | Conn_01x03_Socket

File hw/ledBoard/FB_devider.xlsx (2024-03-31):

U_DAC | 0 | V | min: | 0 | max: | 3.3
U_th_diod | 0.35 | V
V_out_min | 9 | V
V_out_max | 12 | V
 | R | U | I
 | kOhm | V | mA
R1 | 140.00 | 11.2 | 0.08
R2 | 10.00 | 0.8 | 0.08
R3 | 100.33 | 0 | 0
Uout |  | 12

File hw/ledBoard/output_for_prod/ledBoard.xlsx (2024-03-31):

Typ | Osazeno | TME | Mouser nbr. | Id | Designator | Footprint | Quantity | Designation | Supplier and ref
 |  |  |  | 19 | C21,C22 | C_0805_2012Metric_Pad1.18x1.45mm_HandSolder | 2 | C
 |  |  | 6 | 6 | C3,C2 | C_1210_3225Metric_Pad1.33x2.70mm_HandSolder | 2 | 10uF
 |  | obj |  | 3 | C4,C5,C19,C20 | C_0805_2012Metric_Pad1.18x1.45mm_HandSolder | 4 | 0.010uF |  | ++
 |  | obj |  | 1 | C6,C14 | C_0805_2012Metric_Pad1.18x1.45mm_HandSolder | 2 | 6.80nF |  | ++
 |  |  | 7 | 4 | C7,C23,C24,C13 | C_0805_2012Metric_Pad1.18x1.45mm_HandSolder | 4 | 100nF
 |  | obj-0805 |  | 18 | C9,C10,C16,C8,C15,C17 | C_1210_3225Metric_Pad1.33x2.70mm_HandSolder | 6 | 22uF |  | ++
 |  | obj |  | 15 | D2,D4 | D_SOD-523 | 2 | D |  | ++
 |  | obj |  | 5 | J1 | LedBoardPinHeader | 1 | Conn_02x11_Socket
 |  | obj |  | 11 | J2,J3 | JST_XH_B2B-XH-A_1x02_P2.50mm_Vertical | 2 | Conn_01x02
 |  | obj |  | 21 | J8 | PinSocket_1x05_P2.54mm_Vertical | 1 | Conn_01x05_Socket
 |  | obj |  | 22 | J9,J6,J5 | PinSocket_1x03_P2.54mm_Vertical | 3 | Conn_01x03_Socket
 |  | obj |  | 8 | L1,L2 | L_Changjiang_FNR6045S | 2 | 10uH |  | ++
 |  | obj 140k |  | 14 | R1,R9 | R_0805_2012Metric_Pad1.20x1.40mm_HandSolder | 2 | 190k |  | ++
 |  |  | 22 | 12 | R12,R6 | R_0815_2038Metric_Pad1.20x4.05mm_HandSolder | 2 | 10m
 |  |  |  | 17 | R14,R13 | R_0805_2012Metric_Pad1.20x1.40mm_HandSolder | 2 | R
 |  |  | 16 | 13 | R2,R10 | R_0805_2012Metric_Pad1.20x1.40mm_HandSolder | 2 | 10k
 |  | obj |  | 7 | R3,R7 | R_0805_2012Metric_Pad1.20x1.40mm_HandSolder | 2 | 47k |  | ++
 |  | 100k |  | 16 | R4,R11 | R_0805_2012Metric_Pad1.20x1.40mm_HandSolder | 2 | 127k |  | ++
 |  |  | 19 | 10 | R5,R8 | R_0805_2012Metric_Pad1.20x1.40mm_HandSolder | 2 | 100k
 |  |  |  | 2 | U1,U2 | SOT-23-5 | 2 | INA180A4 |  | ++
 |  | obj |  | 9 | U3,U4 | V-DFN3020-13 | 2 | AP63356Q |  | ++

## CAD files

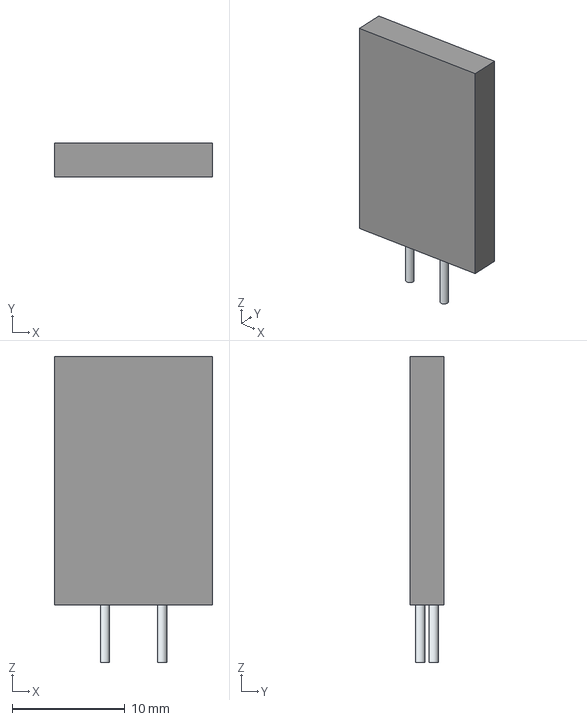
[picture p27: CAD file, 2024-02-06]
hw/parts/LIB_30R400UMR/30R400UMR/3D/30R400UMR.stp
14.0 x 3.00 x 27.1 mm
Leads x 2

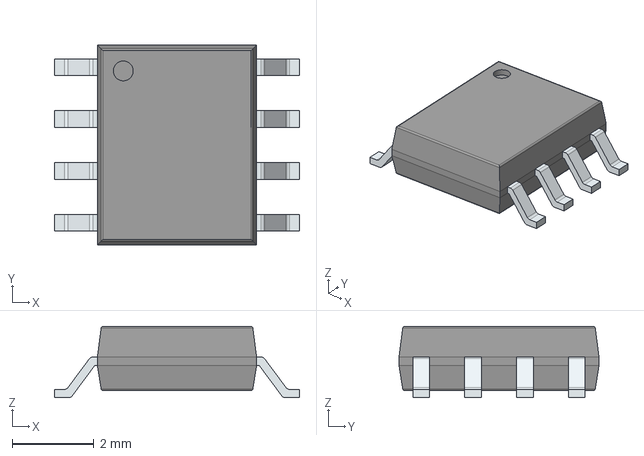
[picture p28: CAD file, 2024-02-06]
hw/parts/LIB_ATA6561-GAQW-N/ATA6561-GAQW-N/3D/ATA6561-GAQW-N.stp
6.00 x 4.90 x 1.75 mm
PinsArrayLR

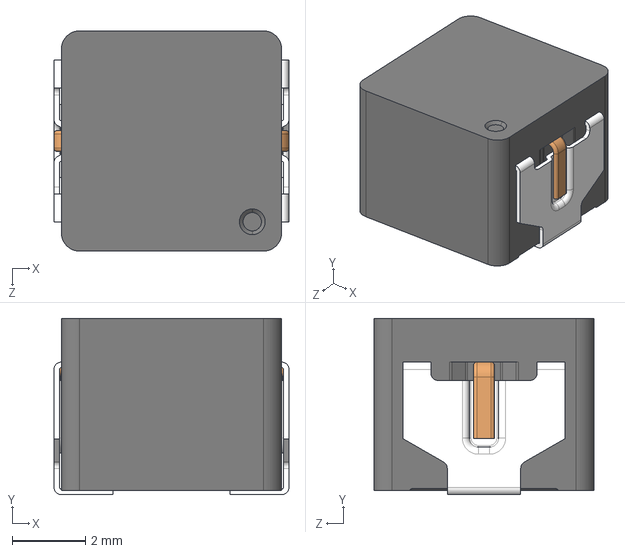
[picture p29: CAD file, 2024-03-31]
hw/parts/LIB_ETQP4M100KFN/ETQP4M100KFN/3D/ETQP4M100KFN.stp
6.40 x 4.80 x 6.00 mm

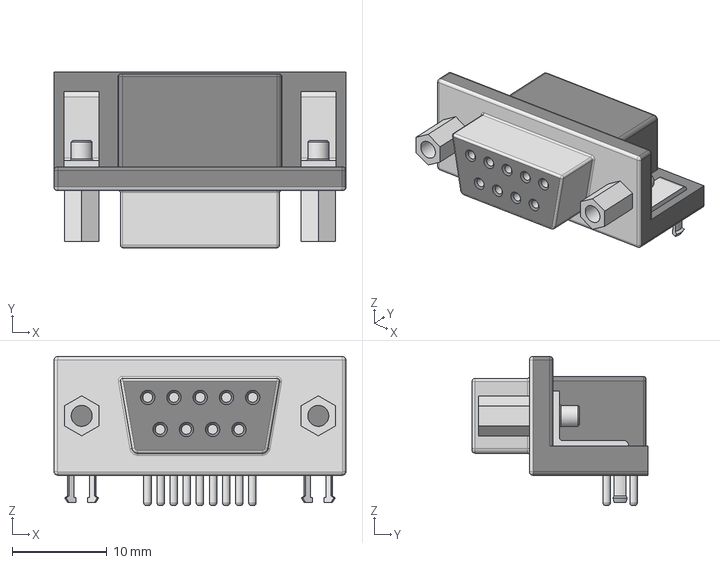
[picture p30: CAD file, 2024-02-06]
hw/parts/LIB_G17C0900132EU/G17C0900132EU/3D/G17C0900132EU.stp
30.8 x 18.6 x 15.8 mm

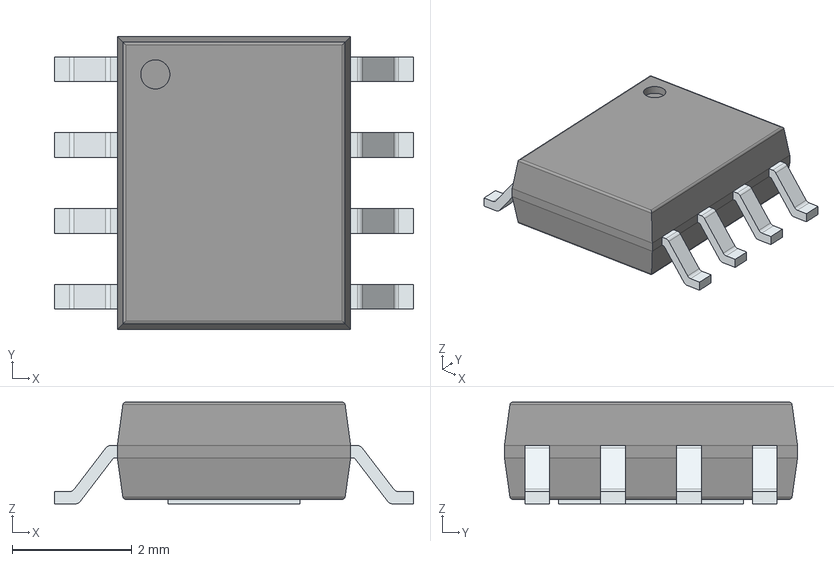
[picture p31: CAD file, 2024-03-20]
hw/parts/LIB_L7986A/L7986A/3D/L7986A.stp
6.00 x 4.90 x 1.70 mm
PinsArrayLR
ThermalPad

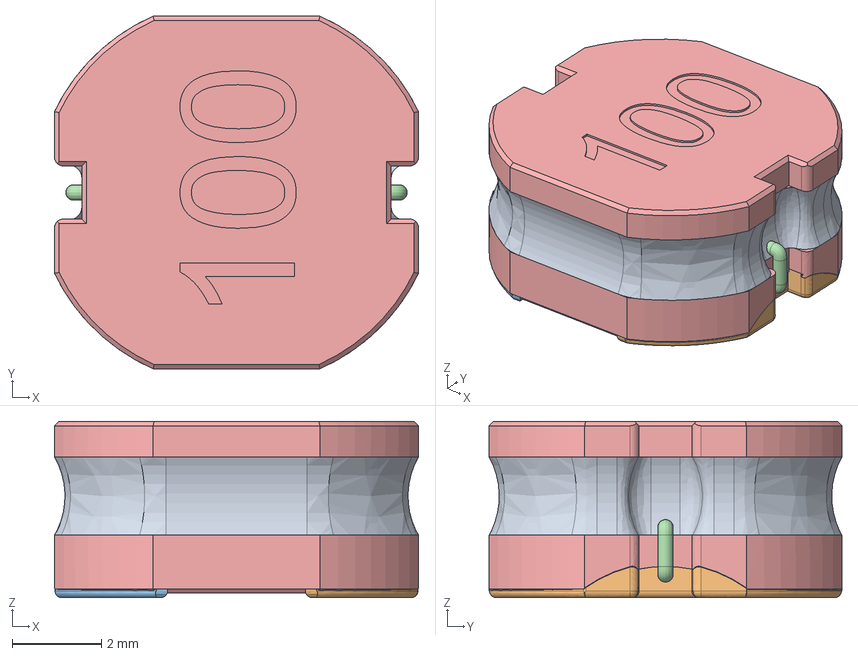
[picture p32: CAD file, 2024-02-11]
hw/parts/LIB_SRN8040-101M/SRN8040-101M/3D/SRN8040-101M.stp
8.15 x 7.90 x 3.95 mm

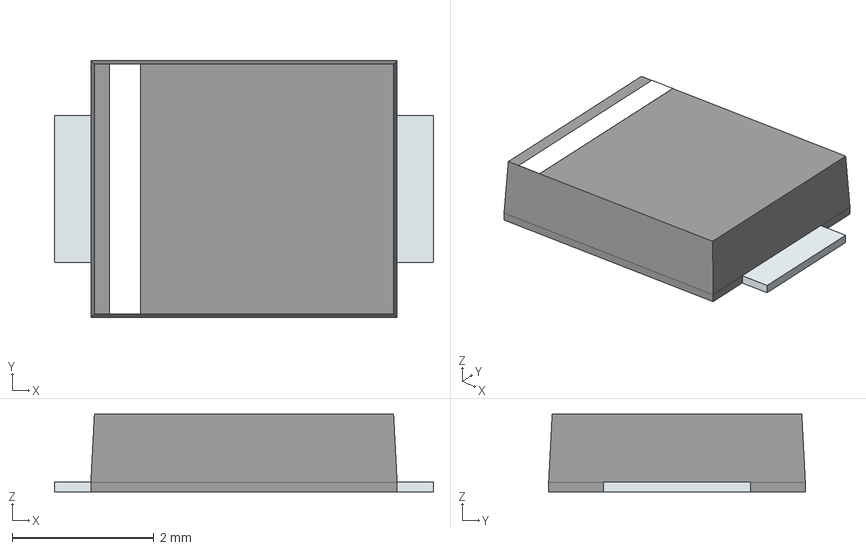
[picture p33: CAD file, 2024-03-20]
hw/parts/LIB_STPS3L40UF/STPS3L40UF/3D/STPS3L40UF.stp
5.35 x 3.62 x 1.10 mm
PinKIdent
PinK
PinA

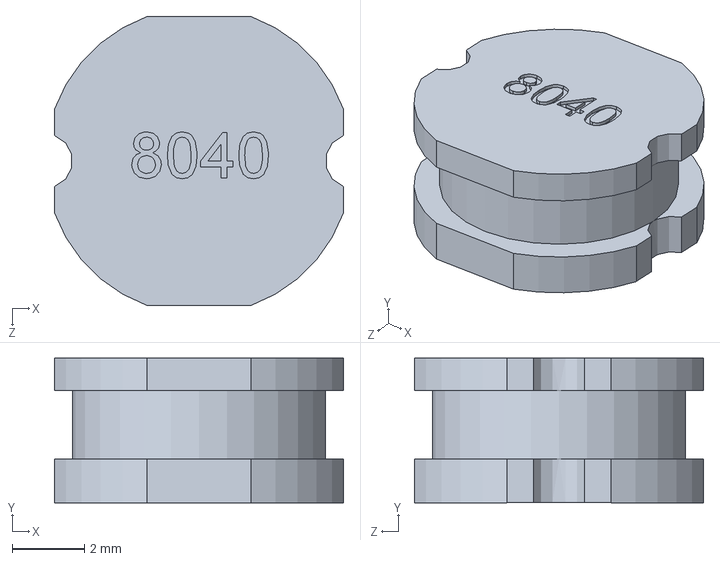
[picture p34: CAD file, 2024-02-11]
hw/parts/SRN8040-101M.SLDPRT
8.00 x 4.01 x 8.00 mm

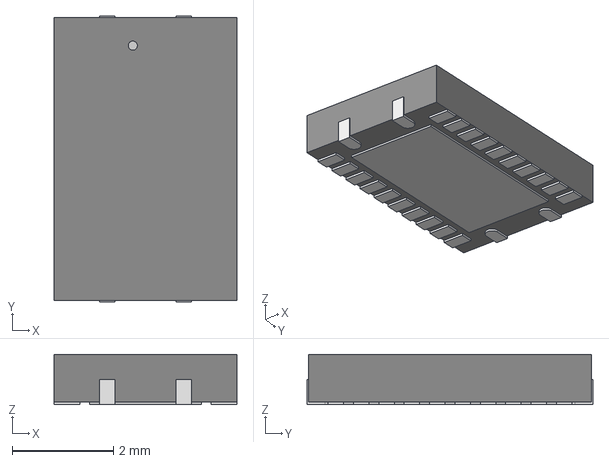
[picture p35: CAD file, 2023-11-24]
hw/parts/ul_LM5148RGYR/VQFN24_RGY_TEX.step
3.61 x 5.64 x 0.993 mm

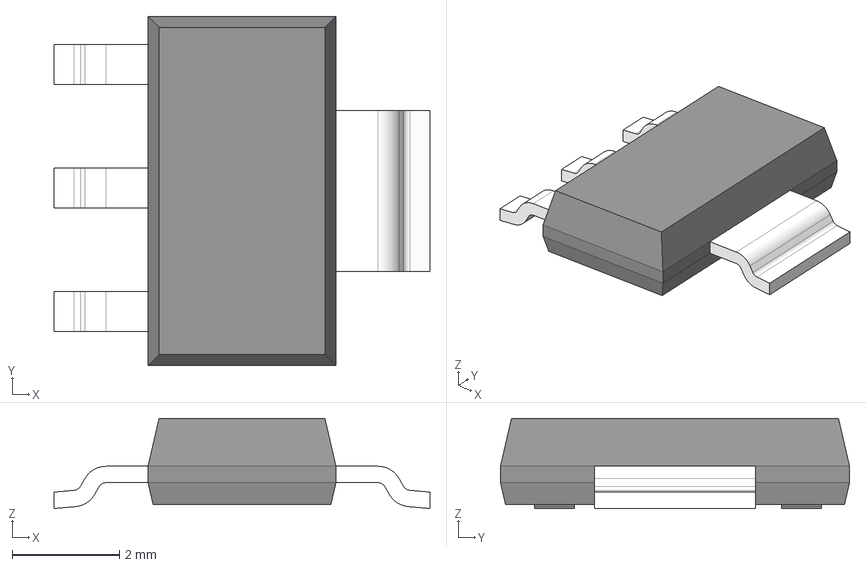
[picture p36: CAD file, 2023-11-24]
hw/parts/ul_PTLV76118DCYR/DCY0004A.stp
7.00 x 6.50 x 1.68 mm
BODY-SOT
LEAD-SOT x 3
LEAD-SOT-WIDE
PIN1-ID

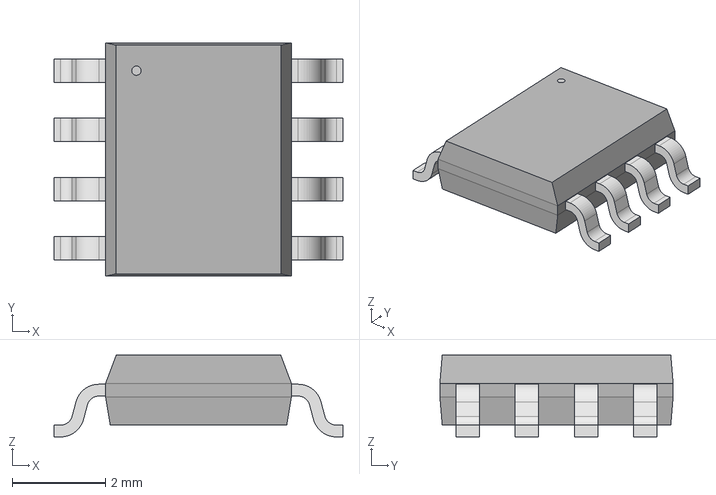
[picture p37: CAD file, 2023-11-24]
hw/parts/ul_SRDA3-3-4DR2G/SOIC8_4X5_ONS.step
6.20 x 5.00 x 1.75 mm

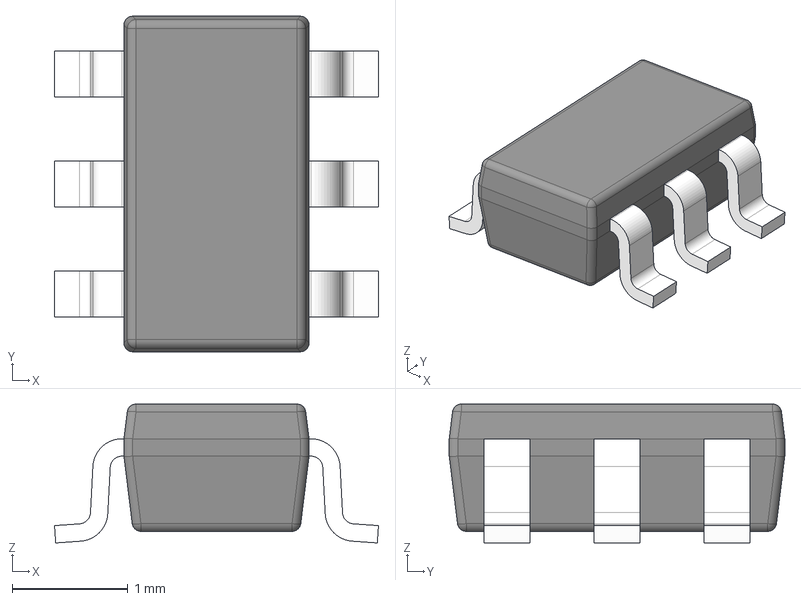
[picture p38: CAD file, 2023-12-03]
hw/parts/ul_TXU0101DBVR/DBV0006A.stp
2.80 x 2.90 x 1.20 mm
BODY-SOT
LEAD-SOT x 6

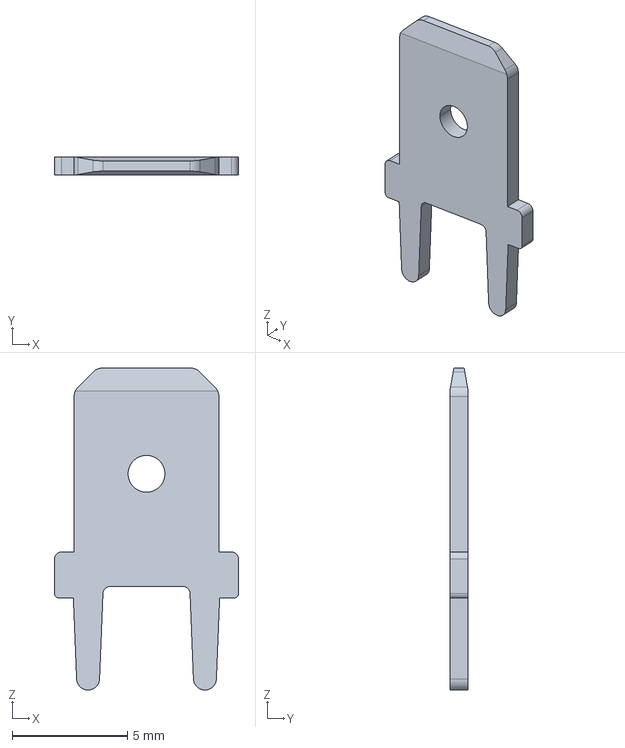
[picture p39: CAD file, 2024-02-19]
hw/parts/LIB_726386-2/726386-2/3D/726386-2.stp
8.00 x 0.8 x 14.0 mm

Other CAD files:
hw/parts/LIB_30R400UMR/30R400UMR/Allegro/30r400umr.psm
hw/parts/LIB_30R400UMR/30R400UMR/DEHDL/30r400umr/chips/chips.prt
hw/parts/LIB_ATA6561-GAQW-N/ATA6561-GAQW-N/Allegro/soic127p600x175-8n.psm
hw/parts/LIB_ATA6561-GAQW-N/ATA6561-GAQW-N/DEHDL/ata6561_gaqw_n/chips/chips.prt
hw/parts/LIB_ETQP4M100KFN/ETQP4M100KFN/Allegro/etq-p4m_kfn.psm
hw/parts/LIB_ETQP4M100KFN/ETQP4M100KFN/DEHDL/etqp4m100kfn/chips/chips.prt
hw/parts/LIB_G17C0900132EU/G17C0900132EU/Allegro/g17c0900132eu.psm
hw/parts/LIB_G17C0900132EU/G17C0900132EU/DEHDL/g17c0900132eu/chips/chips.prt
hw/parts/LIB_SRN8040-101M/SRN8040-101M/Allegro/srn80408r2y.psm
hw/parts/LIB_SRN8040-101M/SRN8040-101M/DEHDL/srn8040_101m/chips/chips.prt

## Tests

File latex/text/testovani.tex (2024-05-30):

\chapter{Sestavení a testování}

Finální fází vývoje je kompletace jednotlivých částí. Pro řídicí jednotku byla zvolena univerzální montážní krabice s~vnějšími rozměry 217x138x\qty{82.2}{mm}. Do čelní strany krabice byly následně vyřezány otvory pro síťové zásuvky a konektory D-sub pro připojení periferí, z boku pak pro napájecí konektor. Také byly vyvrtány otvory odkrývající jednotlivé stavové diody. Byly zvoleny zásuvky přímo určené k~montáži do panelu, navíc jsou vybaveny odklápěcím krytem a těsněním. Díky tomu jsou vhodným kandidátem pro použití v~systému řízení akvária. K~propojení silových vodičů uvnitř šasi bylo použito několik bezšroubových svorkovnic firmy Wago. Tyto svorkovnice jsou již samy o~sobě velmi spolehlivé, i přesto byly pro jistotu zajištěny proti otevření izolační páskou. 

\begin{figure}[h!]
    \centering
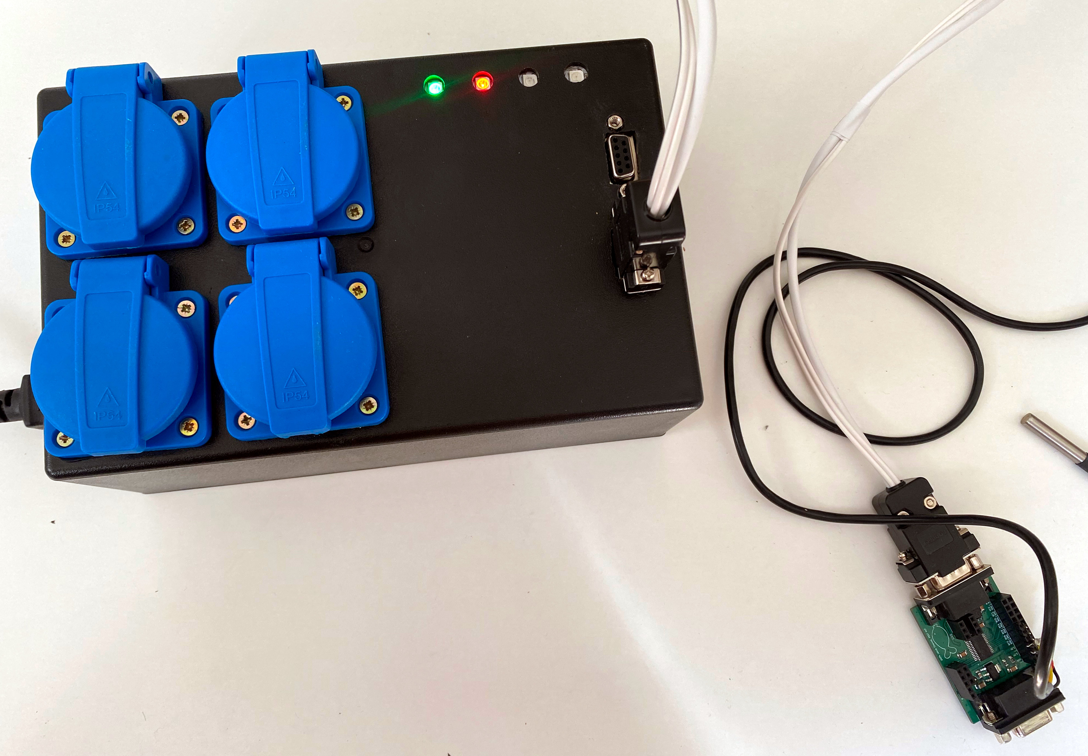
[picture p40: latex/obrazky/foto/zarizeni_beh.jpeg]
    
    \caption{Foto šasi řídicí jednotky v~běhu.}
    \label{fig:obrazky-foto-zarizeni_beh-jpeg}
\end{figure}

Modul externího napájecího zdroje \qty{24}{V} a modul relé jsou pevně připevněny ke stěnám resp. víku krabice. Při návrhu DPS řídicí jednotky byly záměrně zvoleny konektory určené k~montáži do panelu, při finálním sestavení zařízení však bylo zjištěno, že tloušťka stěny krabice je příliš velká a konektory takto uchyceny být nemohou. V~tuto chvíli je tedy DPS upevněna pouze provizorně. Možných řešení tohoto problému je několik, jako nejelegantnější se jeví použití metody 3D tisku. Do pravé části šasi bude vyřezán větší otvor, který bude celý překryt vytištěným panelem. Navržený panel pak bude disponovat vhodnějšími otvory pro uchycení konektorů D-sub, bude nabízet prostor pro již instalovaný LED pásek a také pro displej, který je plánovaným rozšířením zařízení.  

\begin{figure}[h!]
    \centering
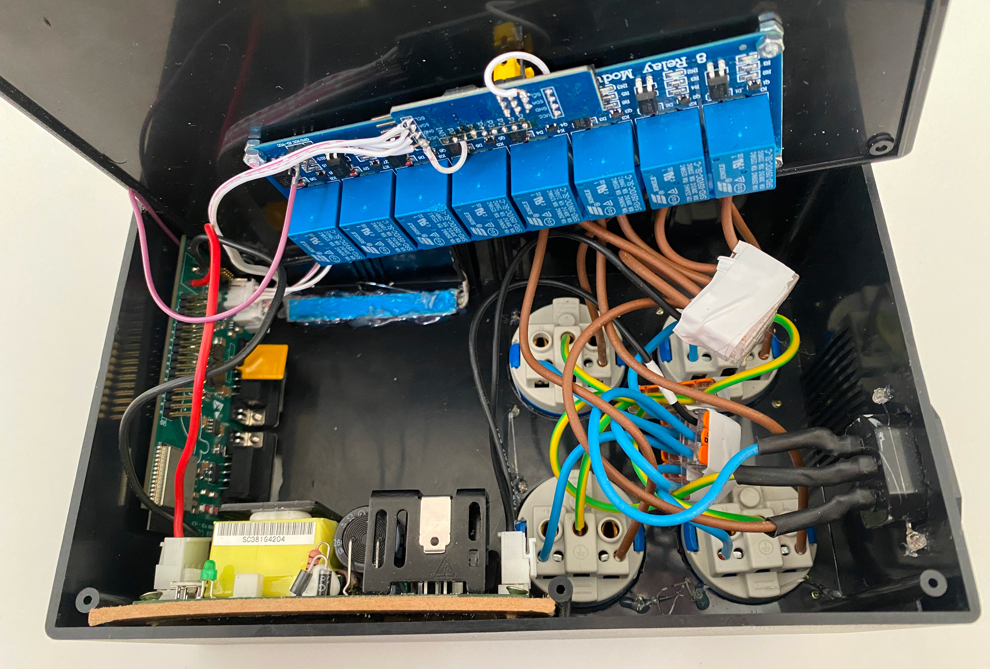
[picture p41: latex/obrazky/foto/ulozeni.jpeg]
    
    \caption{Pohled dovnitř šasi řídicí jednotky.}
    \label{fig:obrazky-foto-ulozeni-jpeg}
\end{figure}

Výsledný vzhled zařízení je zachycen na obr.~\ref{fig:obrazky-foto-zarizeni_beh-jpeg}, pohled dovnitř šasi řídicí jednotky je pak možný na obr.~\ref{fig:obrazky-foto-ulozeni-jpeg}.

\section{Testování a nalezené chyby}
    Vývoj a prvotní testy zařízení probíhaly mimo samotné šasi. Namísto externího napájecího modulu byl využíván laboratorní zdroj a řídicí jednotka i moduly periferií byly rozloženy na stole, aby byly snadno dostupné pro programování. V~této konfiguraci byla testována funkce jednotlivých modulů připojených jak samostatně, tak i společně ve stejnou dobu. Systém byl od počátku navrhován tak, aby veškerá konfigurace systému bylo prováděna přes webové rozhraní. Toto rozhodnutí mírně komplikovalo samotné testování funkce zařízení. Před samotným testováním totiž musela být vyvinuta alespoň provizorní webová aplikace a naprogramována spolehlivá komunikace se serverem. Tyto kroky pak zabraly mnohem více času, než byl původní předpoklad. V~průběhu vývoje bylo také postupně objeveno několik různě závažných návrhových chyb týkajících se hardwaru. 
    
    Nejvíce problémů se týká modulu LED osvětlení. Při návrhu byl položen špatný předpoklad pro minimální napětí LED pásků. Při napětí vypočteném v~rovnici~\ref{rovnice:led_modul} LED diody stále docela výrazně svítí a pro jejich plné zhasnutí je potřeba napětí přibližně o~\qty{1}{V} nižší. Tento problém je snadno řešitelný výměnou jednoho z~rezistorů děliče. Dalším problémem byl špatně zvolený pin mikrokontroléru. Periferie DAC jako jediná neumožňuje nastavení vlastního výstupního pinu a je pevně vázaná na dva konkrétní piny, musela tedy být zavedena drátová propojka. Jeden ze dvou navržených měničů napětí nefunguje vůbec a příčina tohoto problému prozatím nebyla odhalena, je tedy možné využít pouze jeden kanál svícení. 

    Poslední problém se vyskytl až při montáži řídicí jednotky do krabice. Při nahrazení laboratorního zdroje externím modulem nastává problém se startem procesoru řídicí jednotky. Procesor se nezapne korektně a je potřeba stisknout resetovací tlačítko, pak již vše funguje jak má. Na vině je pravděpodobně jiná doba náběhu napájení, která má za následek nedodržení časování popsaného v~kapitole~\ref{sec:ridici-jendotka-esp32-modul}. 

    Dokud nebudou všechny tyto problémy odstraněny a zařízení dostatečně otestováno v~simulovaných podmínkách, nebylo by vhodné provádět test za reálného provozu. Akvarijní ryby by byly vystaveny nechtěnému stresu nebo by v~horším případě některá důležitá část systému vypověděla funkci. 

\section{Návrh budoucích vylepšení}
    Ačkoliv se za výrobkem skrývá velká spousta práce, ne všechny stanovené cíle byly dosaženy. V~tuto chvíli se jedná o~prototyp, který demonstruje funkci a možnosti zařízení, ne však zcela bezchybně. Ze zmíněných požadavků např. nebyla implementována možnost vzdálené aktualizace firmwaru. Samotné stažení firmwaru by v~tuto chvíli nebyl problém, jelikož komunikace se serverem je  implementována poměrně dobře. Je však potřeba zajistit, aby aktualizací nebyla narušena kompatibilita s~připojenými periferiemi nebo rozhraním API. Pro spolehlivou implementaci této funkce tak bude potřeba daleko více času. Co se týče řídicí jednotky, je v~plánu vybavit ji také malým displejem, který může nést více informací než stavové diody. Např. by bylo užitečné znát počet detekovaných periferií a informovat uživatele o~úspěšném připojení nového modulu. 

    Díky modulární architektuře bude poměrně jednoduché systém rozšířit o~spoustu dalších funkcí, které se ukáží jako potřebné. Vizí blízké budoucnosti je dokončení sensoru pH a automatického krmítka.

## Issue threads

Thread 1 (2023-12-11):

Ošetření zkratu mezi 24V a 5.2V na konektoru.

charvotj, 2023-12-11:
Při zkratu by v současné chvíli nejspíš došlo k odpálení všech LDO pro jednotlivé MCU a možná i samotných MCU, což by bylo asi nemilé. Možným řešením je za mě asi TLD nebo Zenerova dioda mezi 5.2V a GND + polyfuse na 5.2V.

Potřeba zkonzultovat a najít vhodnou součástku.

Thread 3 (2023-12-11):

Relé modul - dotazy, postřehy

charvotj, 2023-12-11:
Dořešit otázku řídícího napětí 3.3 vs 5V.
scénář: pin ->i2c -> gpio expander -> optoclen -> rele
...Buď bude stačit všude 3,3V a nebo někde po cestě změna na 5V

Jak je to s galvanickým oddělením? Je optočlen dostatečný a je nějaká ochrana i na VCC pinu?

Alternativa dostat všechny relé přímo na vlastní desku i s gpio expandérem.

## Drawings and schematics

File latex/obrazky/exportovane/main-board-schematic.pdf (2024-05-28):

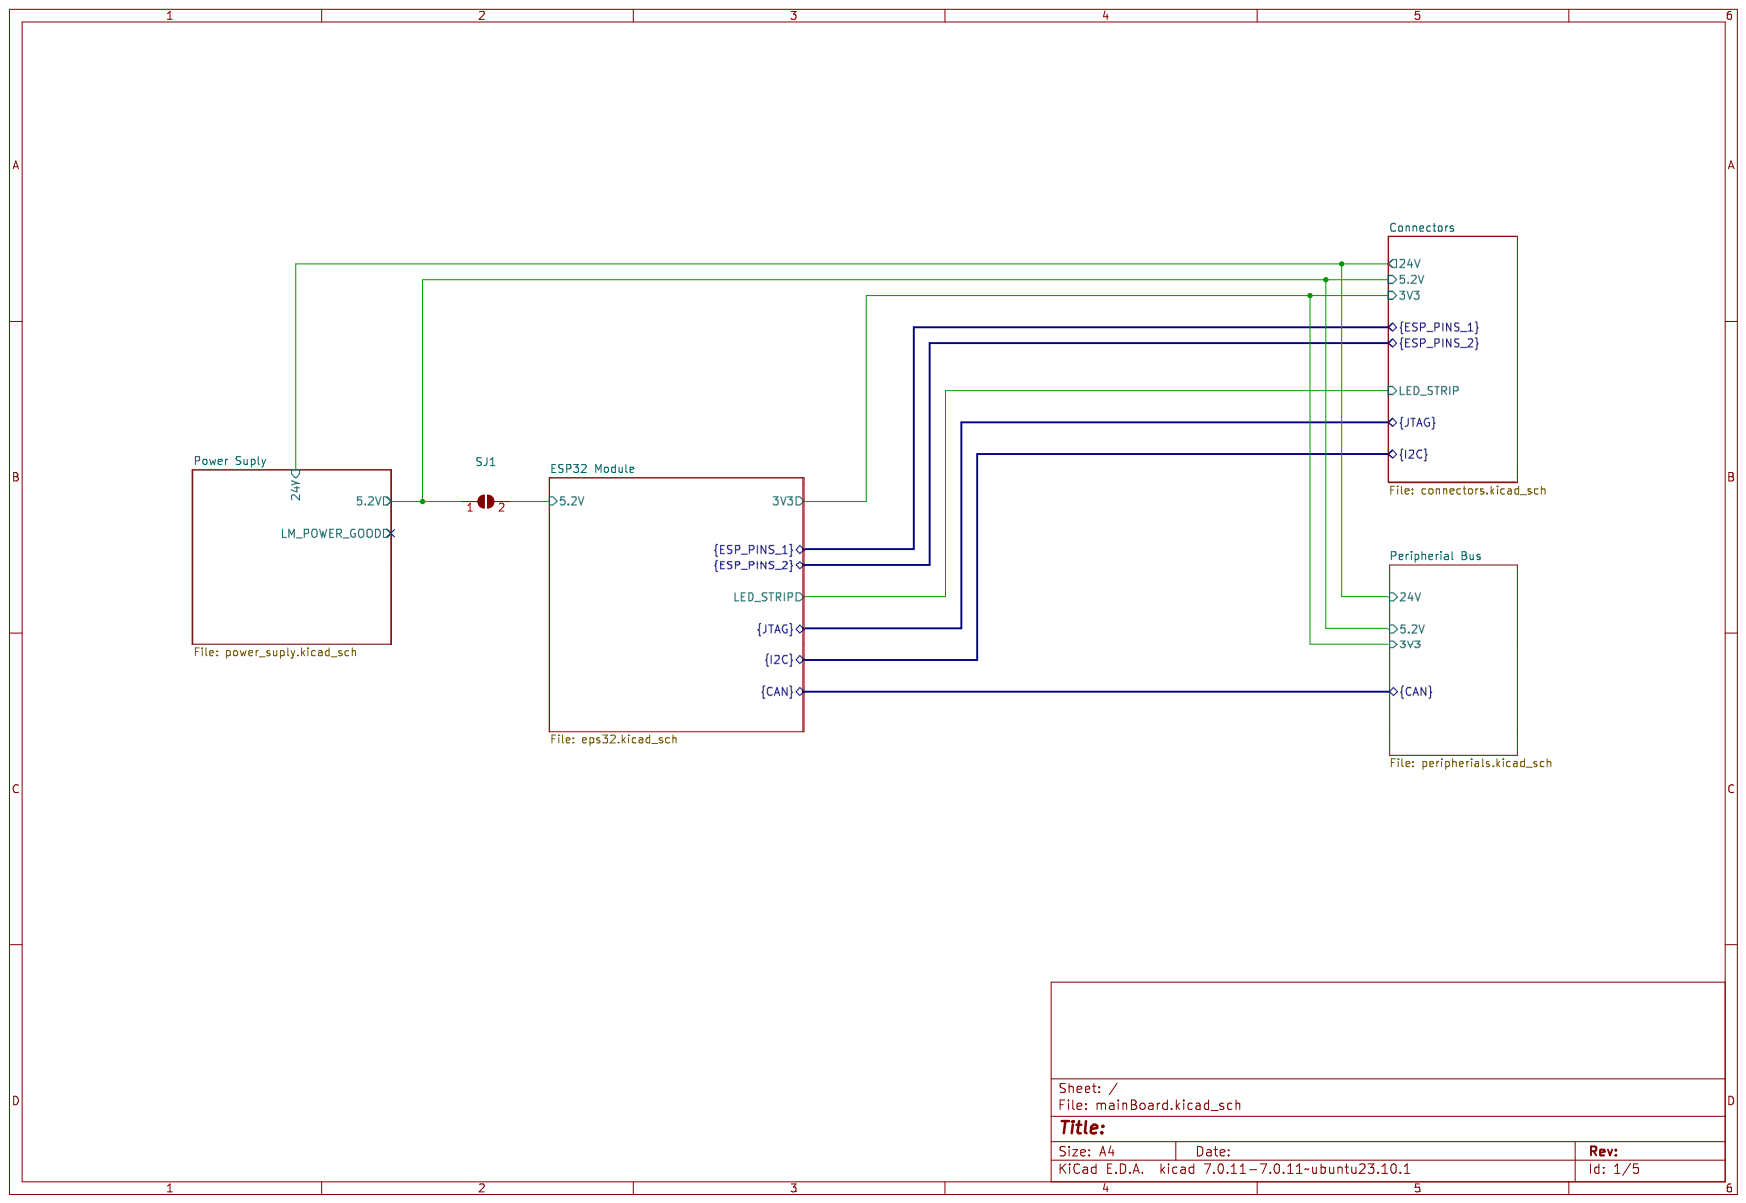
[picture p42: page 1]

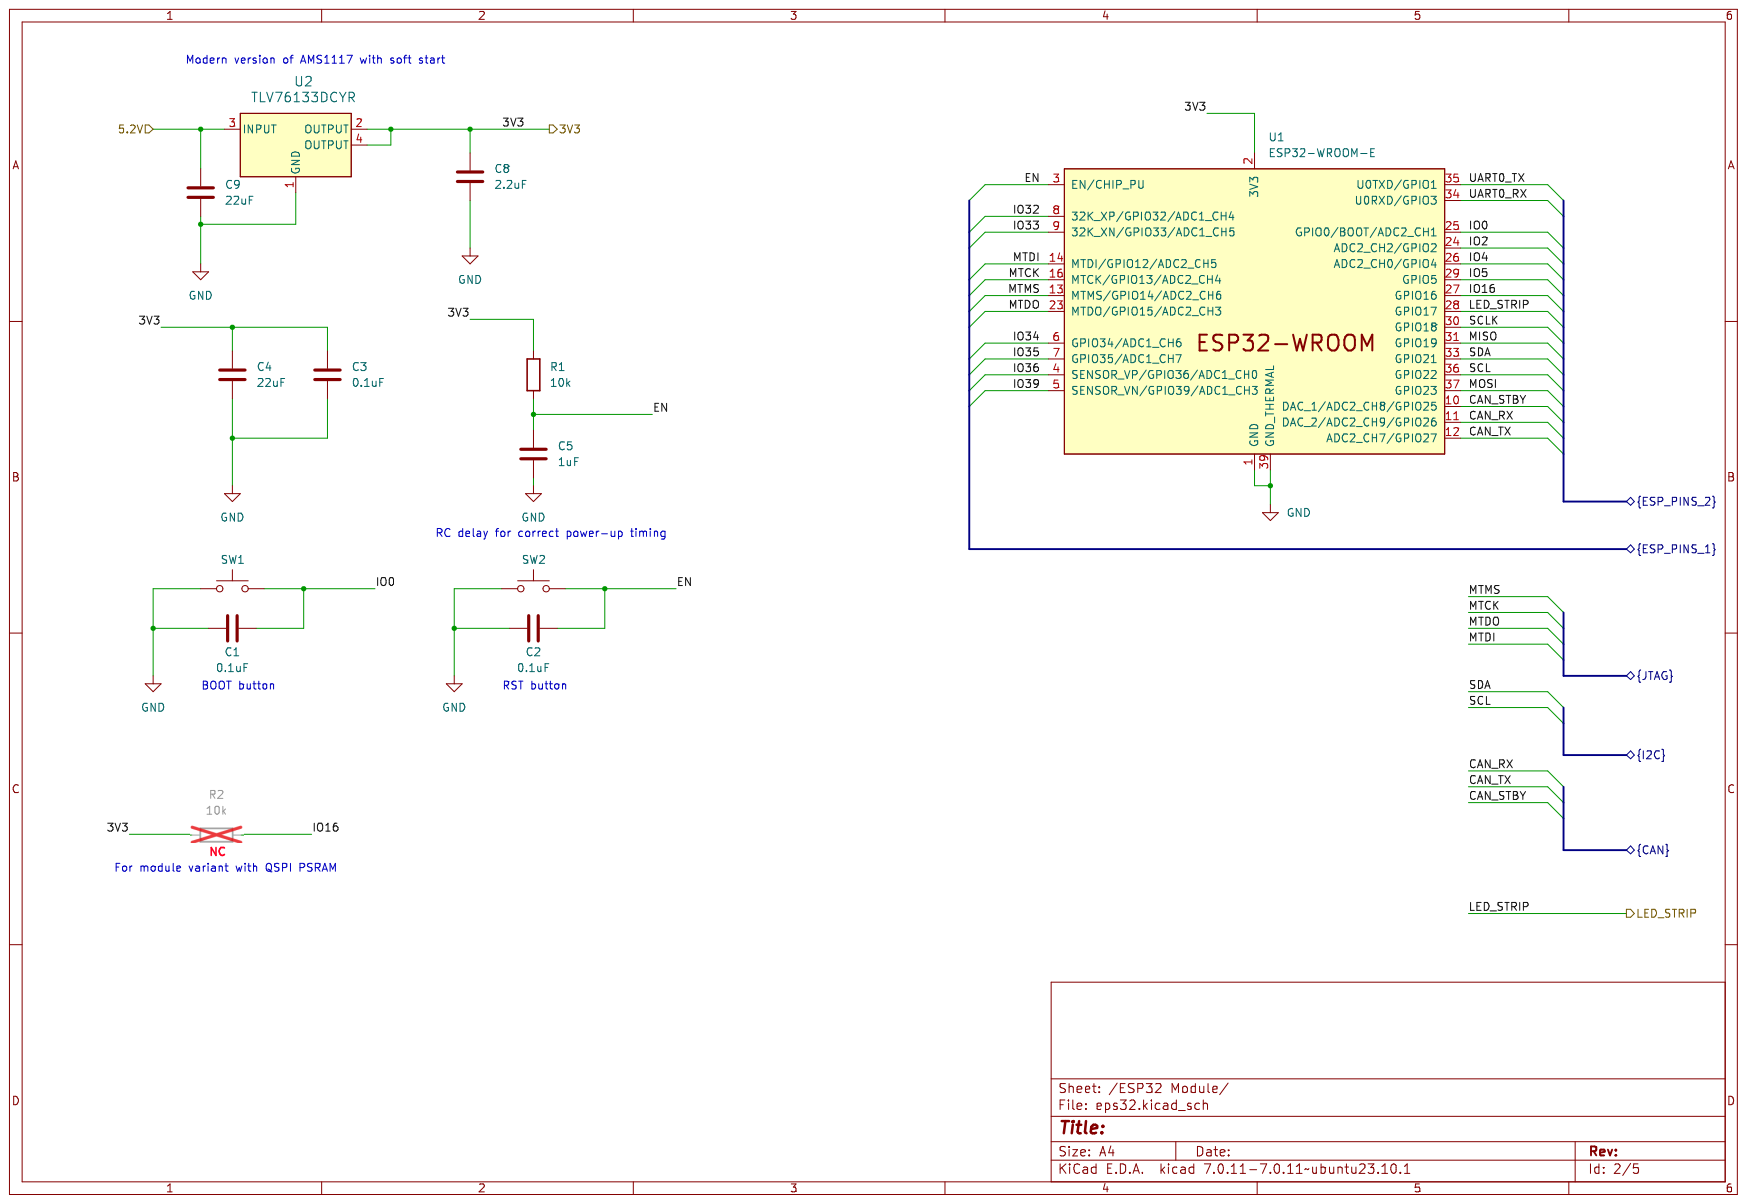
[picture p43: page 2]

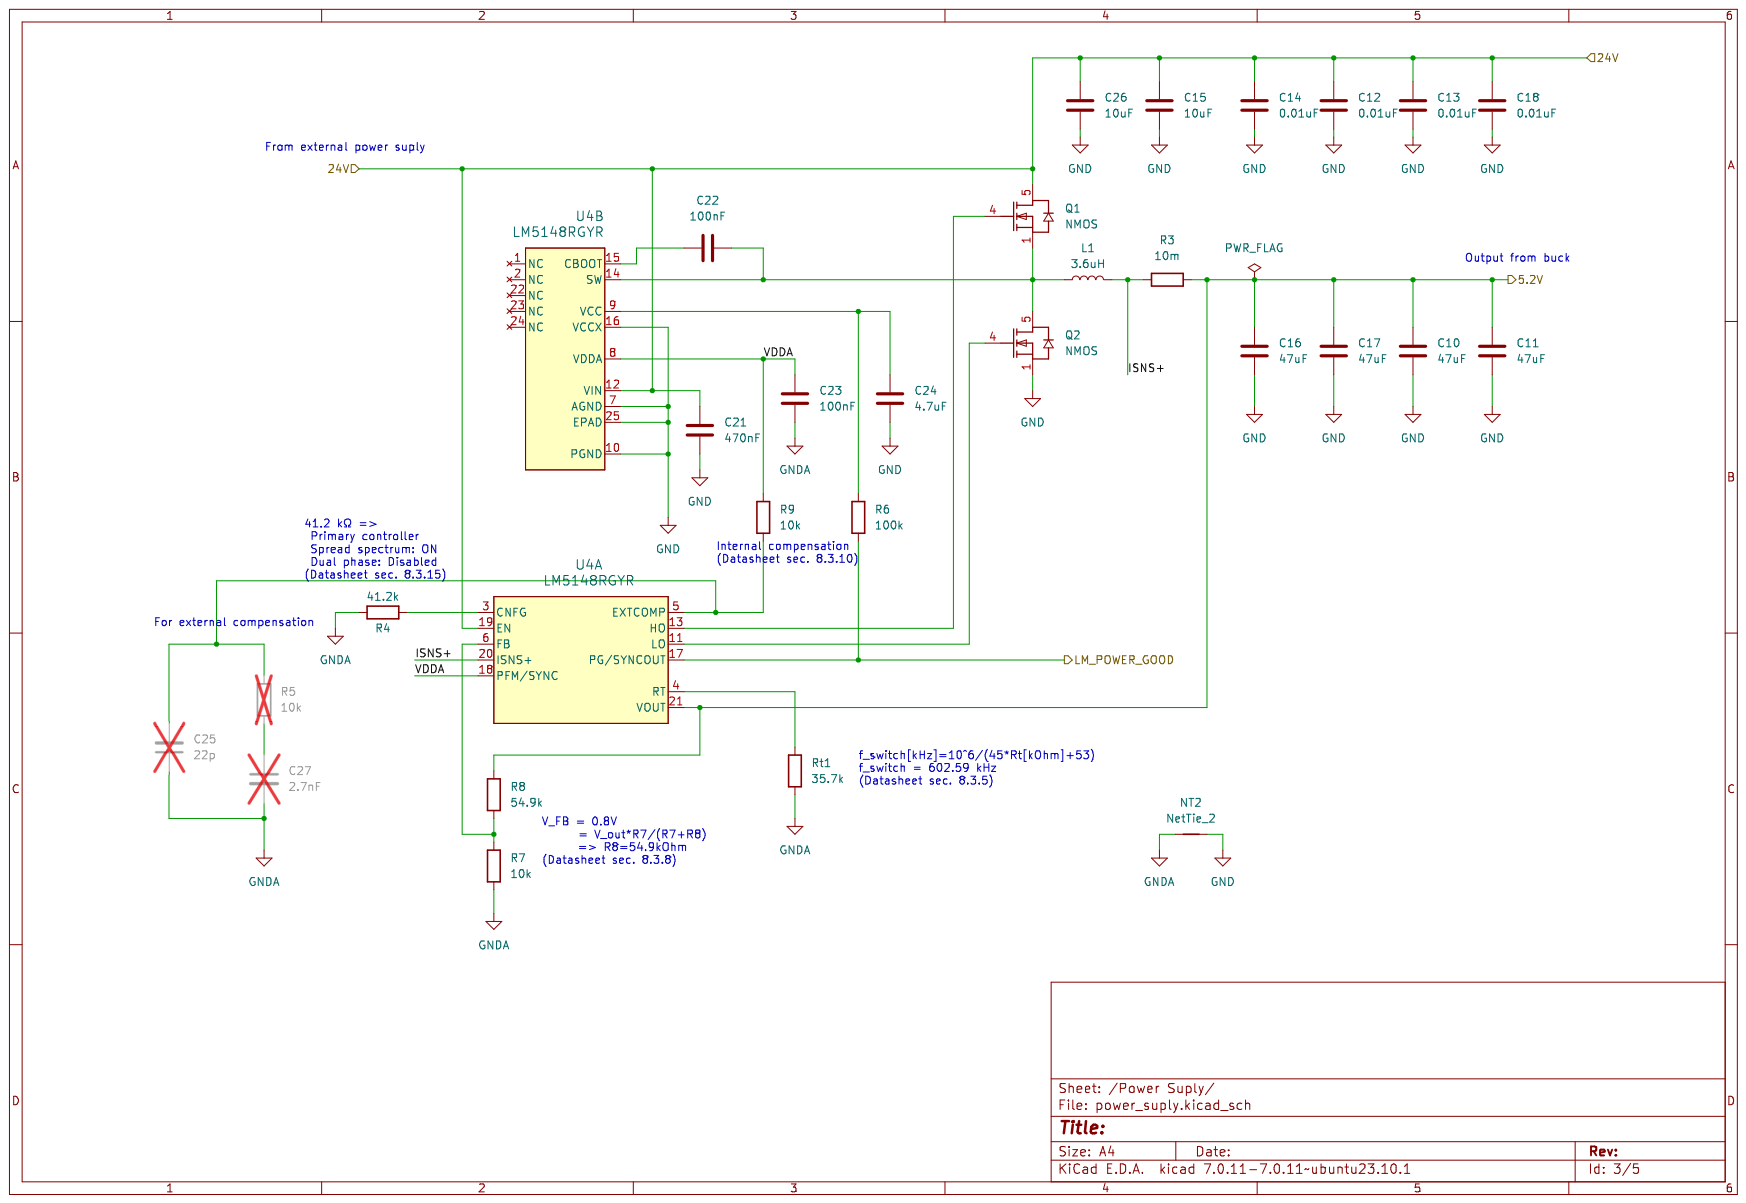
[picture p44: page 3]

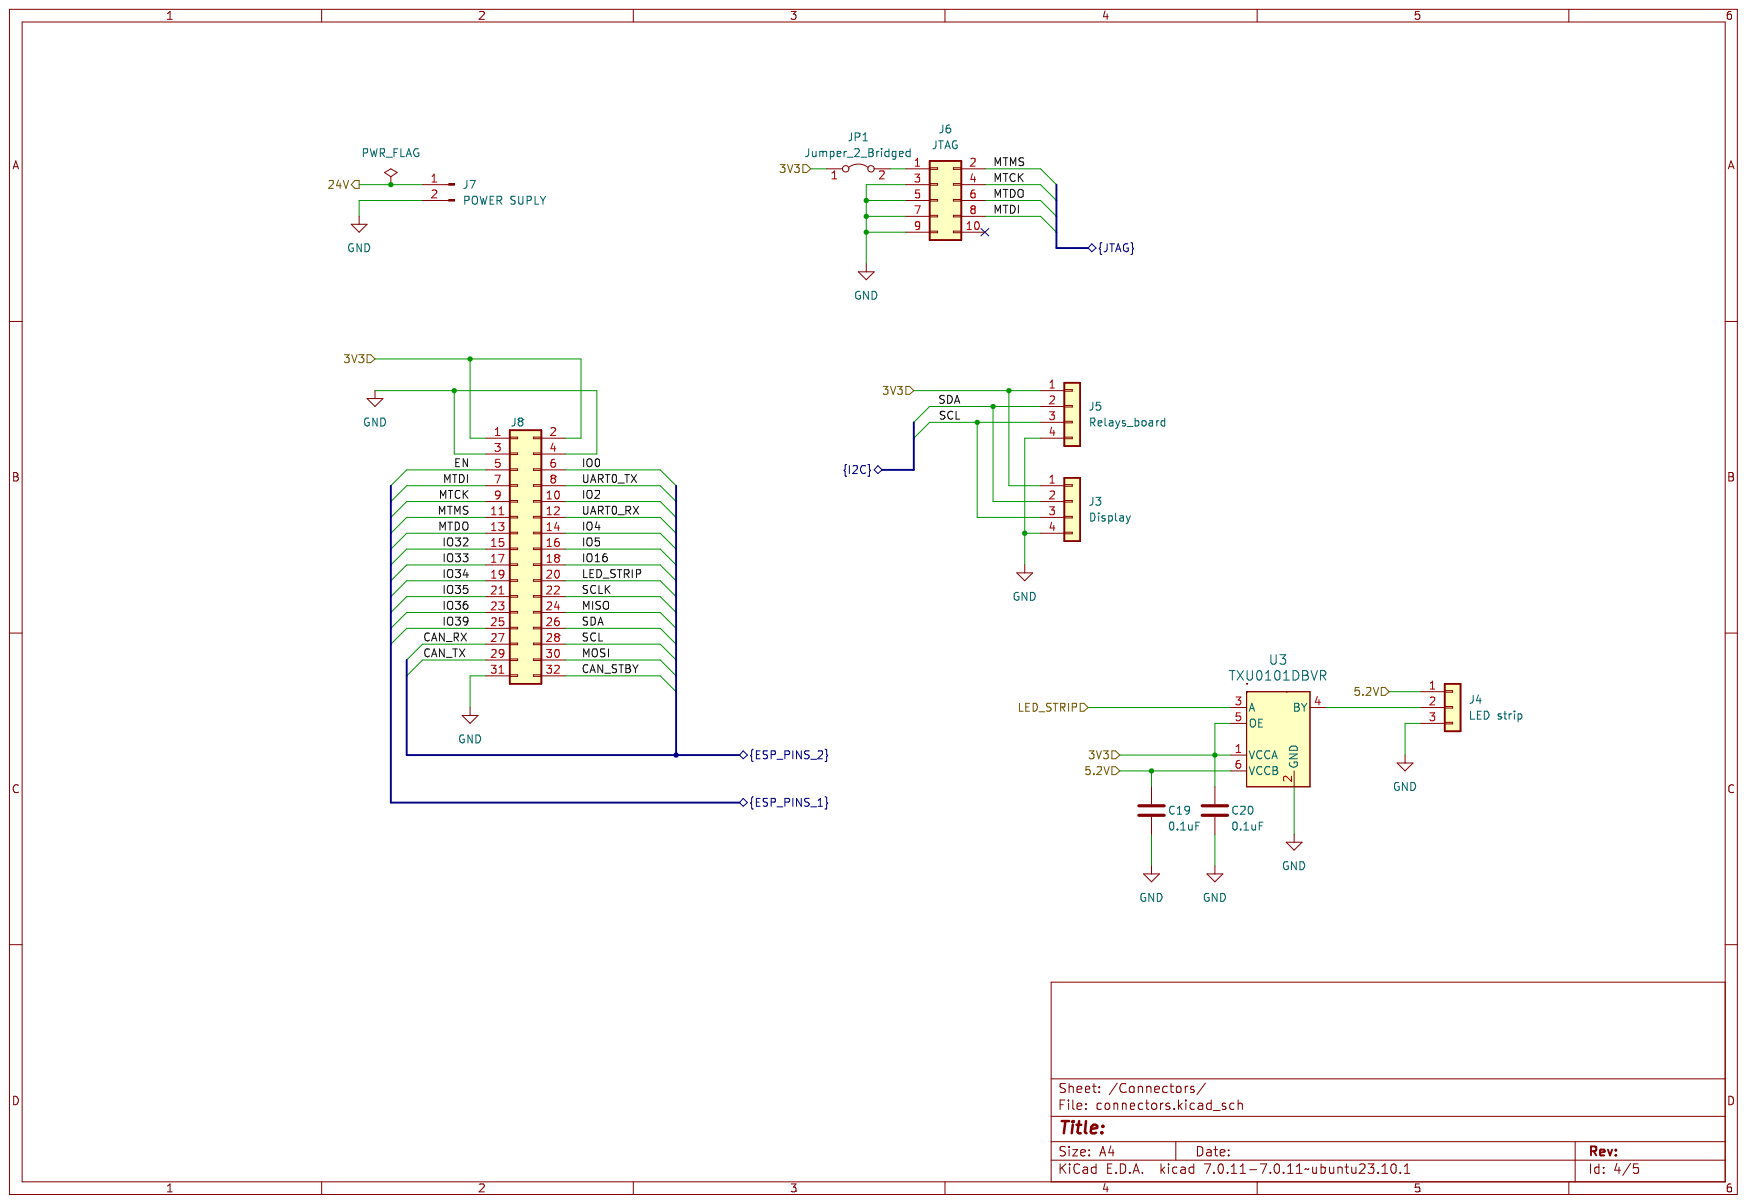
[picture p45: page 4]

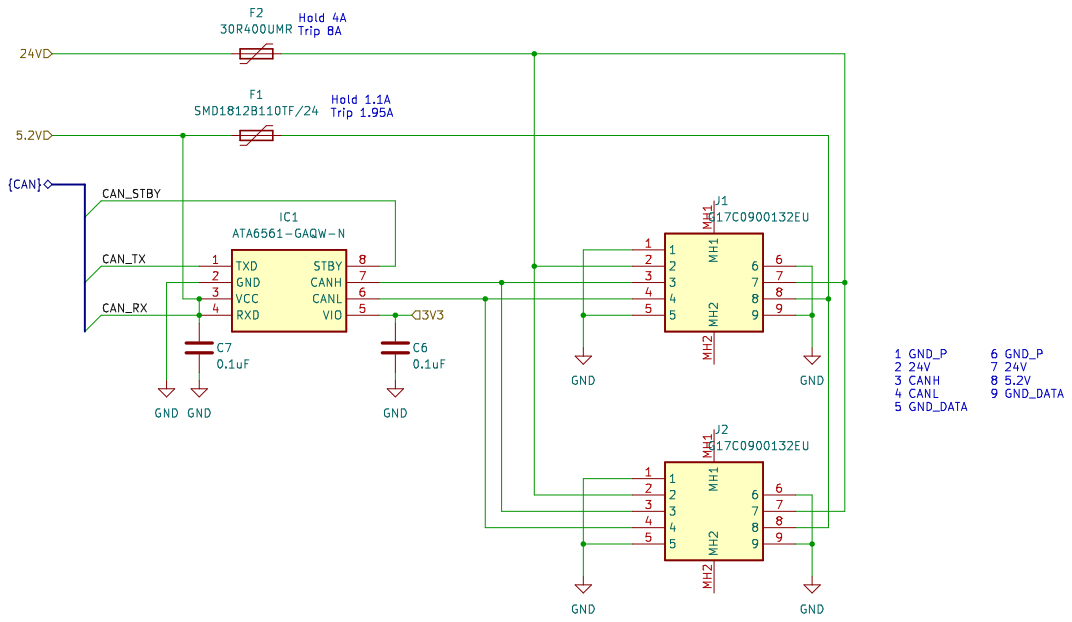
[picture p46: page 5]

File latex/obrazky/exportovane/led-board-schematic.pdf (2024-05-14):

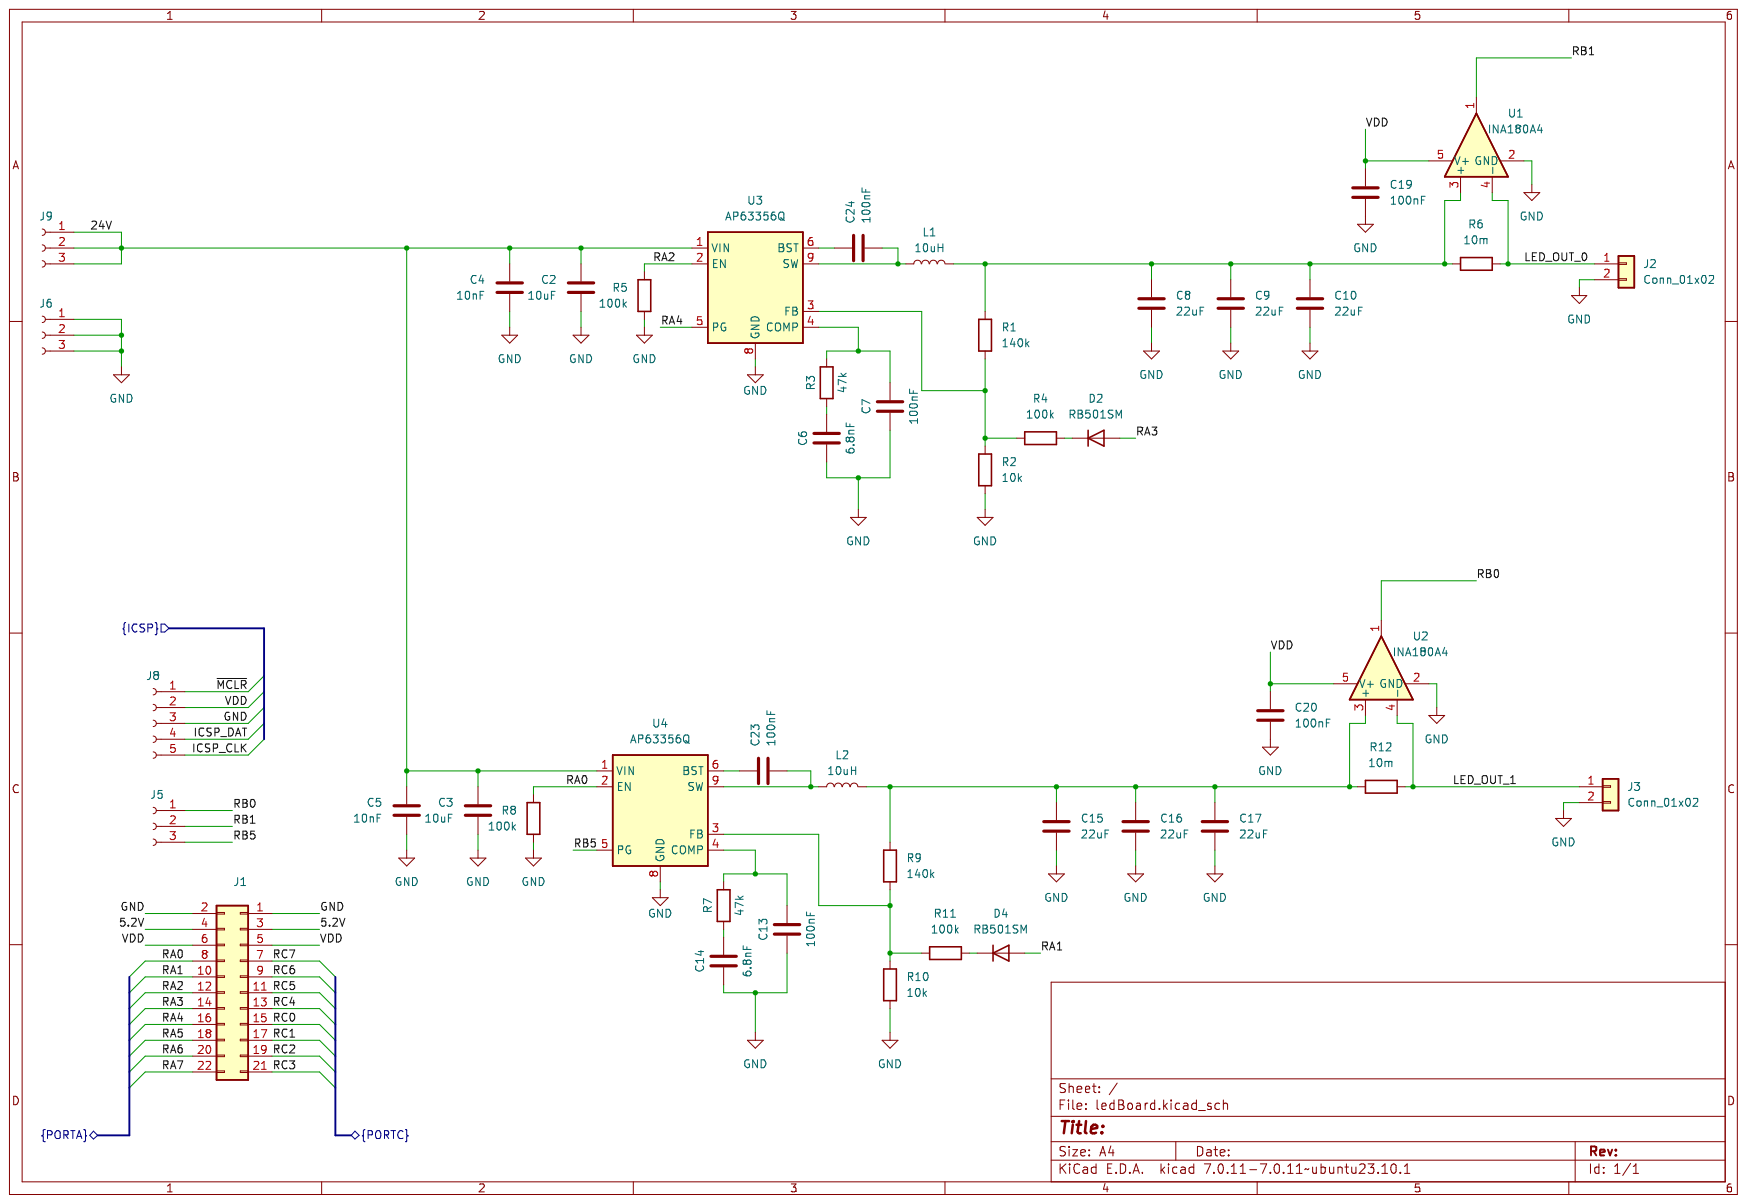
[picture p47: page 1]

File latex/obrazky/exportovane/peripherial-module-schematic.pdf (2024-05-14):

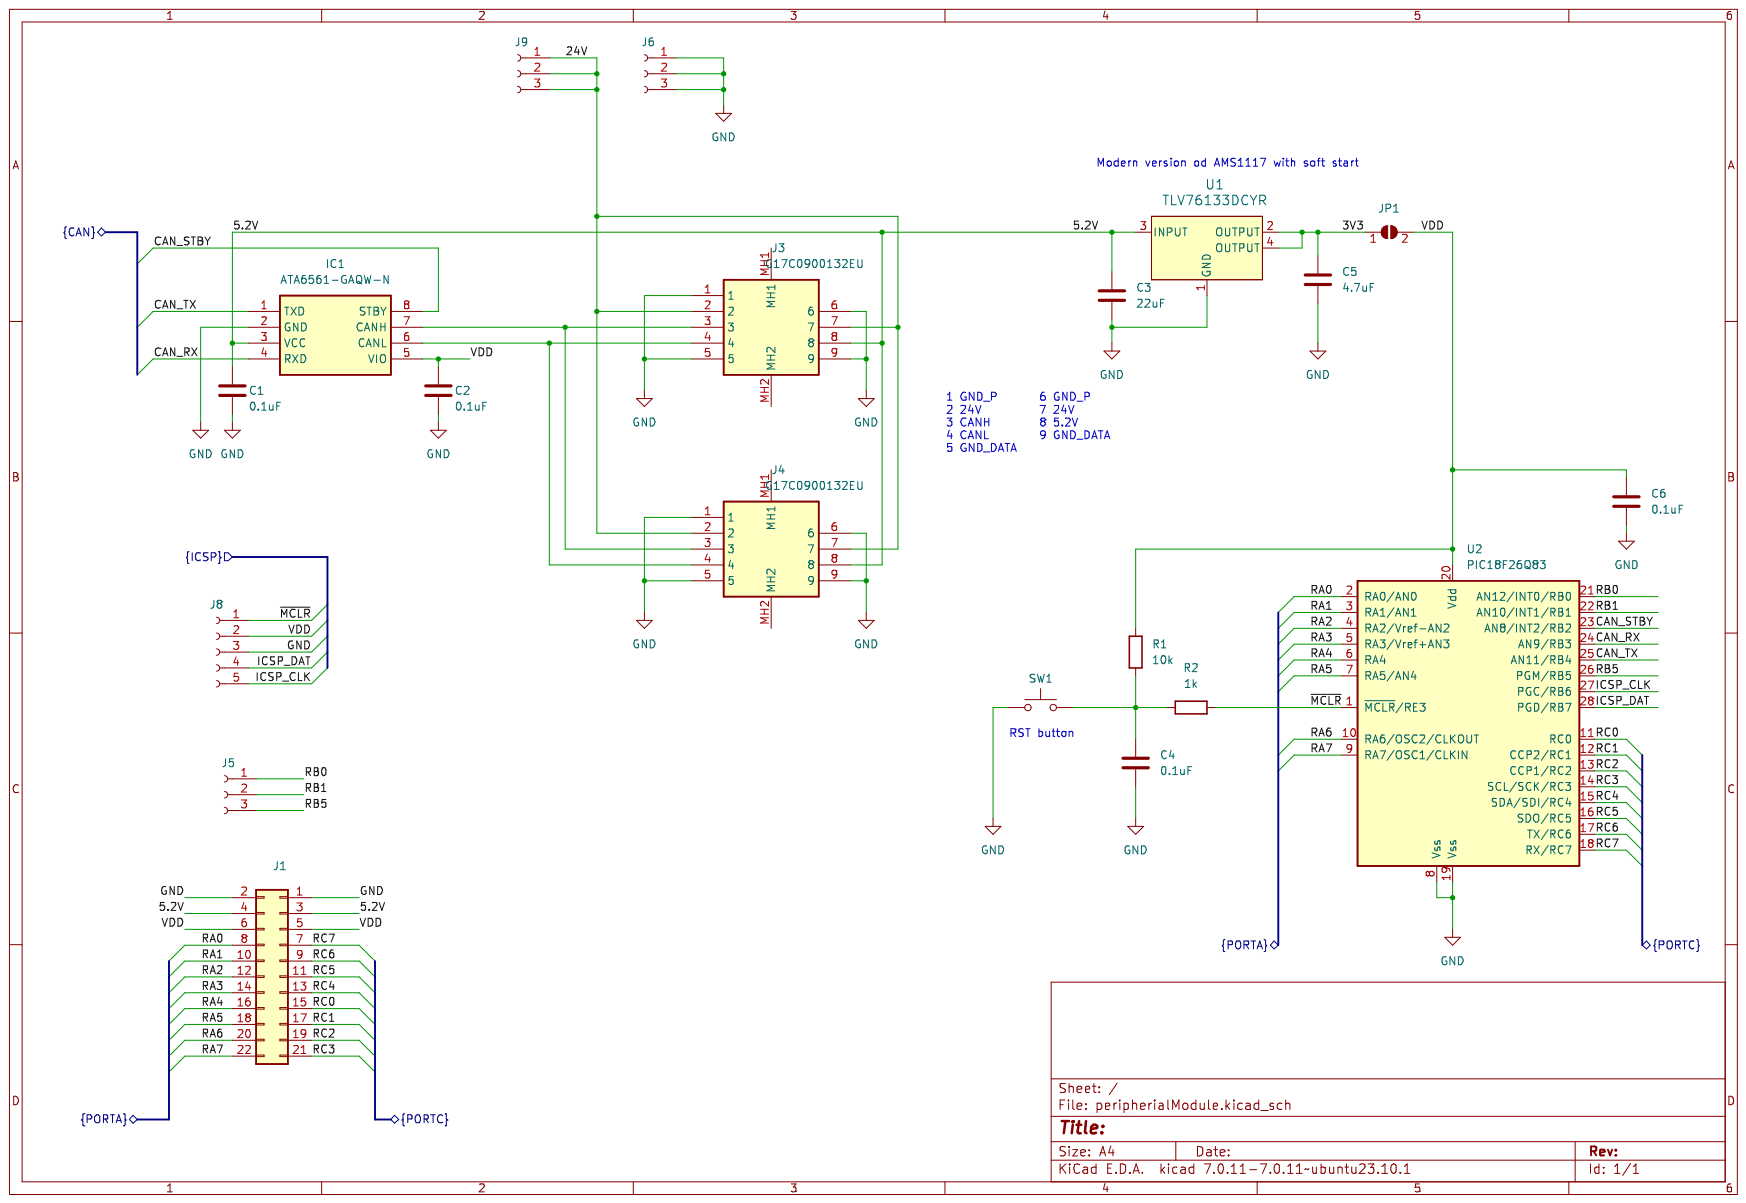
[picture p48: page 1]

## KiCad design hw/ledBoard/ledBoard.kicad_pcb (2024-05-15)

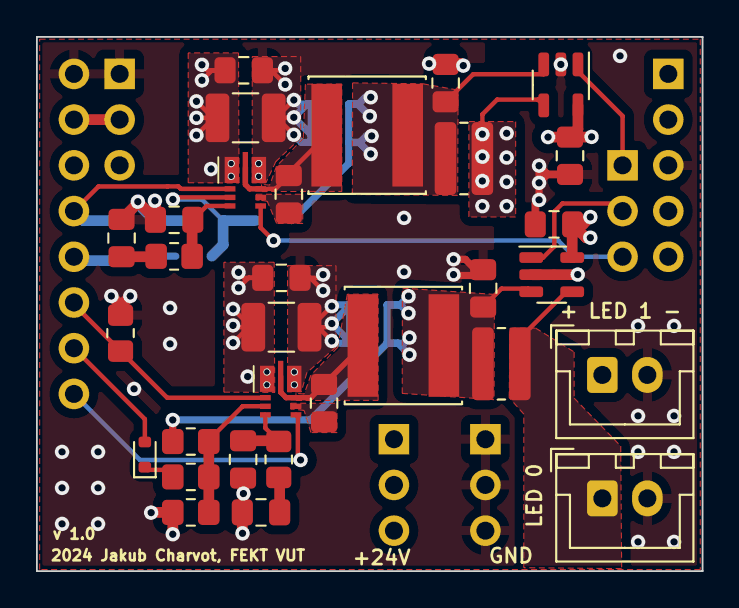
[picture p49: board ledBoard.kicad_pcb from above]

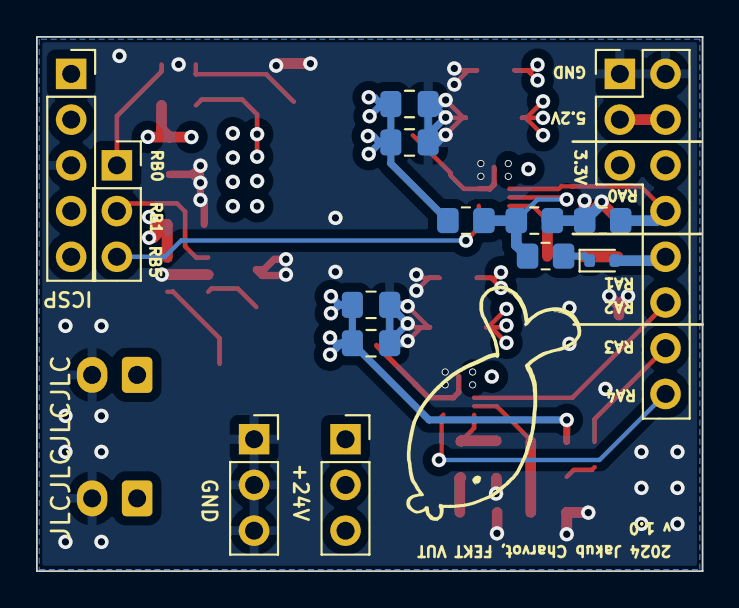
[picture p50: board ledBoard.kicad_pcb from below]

Board: 4 copper layers, 37.0 x 29.7 mm, 45 parts (13 on the bottom side), 28 nets.

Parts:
C2, C3: 10uF; C_1210_3225Metric_Pad1.33x2.70mm_HandSolder
C4, C5: 10nF; C_0805_2012Metric_Pad1.18x1.45mm_HandSolder
C6, C14: 6.8nF; C_0805_2012Metric_Pad1.18x1.45mm_HandSolder
C7, C13, C19, C20, C23, C24: 100nF; C_0805_2012Metric_Pad1.18x1.45mm_HandSolder
C8, C9, C10, C15, C16, C17: 22uF; C_0805_2012Metric_Pad1.18x1.45mm_HandSolder
D2, D4: RB501SM; D_SOD-523
J1: Conn_02x11_Socket; LedBoardPinHeader
J2, J3: Conn_01x02; JST_XH_B2B-XH-A_1x02_P2.50mm_Vertical
J5, J6, J9: Conn_01x03_Socket; PinSocket_1x03_P2.54mm_Vertical
J8: Conn_01x05_Socket; PinSocket_1x05_P2.54mm_Vertical
L1, L2: 10uH; L_Changjiang_FNR6045S
R1, R9: 140k; R_0805_2012Metric_Pad1.20x1.40mm_HandSolder
R2, R10: 10k; R_0805_2012Metric_Pad1.20x1.40mm_HandSolder
R3, R7: 47k; R_0805_2012Metric_Pad1.20x1.40mm_HandSolder
R4, R5, R8, R11: 100k; R_0805_2012Metric_Pad1.20x1.40mm_HandSolder
R6, R12: 10m; R_0815_2038Metric_Pad1.20x4.05mm_HandSolder
U1, U2: INA180A4; SOT-23-5
U3, U4: AP63356Q; V-DFN3020-13

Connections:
/5.2V: J1.3, J1.4
/24V: C2.1, C3.1, C4.1, C5.1, J9.1, J9.2, J9.3, U3.1 (VIN), U4.1 (VIN)
/LED_OUT_0: J2.1, R6.1, U1.4 (-)
/LED_OUT_1: J3.1, R12.1, U2.4 (-)
/RA0: J1.8, R8.1, U4.2 (EN)
/RA1: D4.2 (A), J1.10
/RA2: J1.12, R5.1, U3.2 (EN)
/RA3: D2.2 (A), J1.14
/RA4: J1.16, U3.5 (PG)
/RB0: J5.1, U2.1
/RB1: J5.2, U1.1
/RB5: J5.3, U4.5 (PG)
/VDD: C19.1, C20.1, J1.5, J1.6, J8.2, U1.5 (V+), U2.5 (V+)
GND: C2.2, C3.2, C4.2, C5.2, C6.1, C7.1, C8.2, C9.2, C10.2, C13.1, C14.1, C15.2, C16.2, C17.2, C19.2, C20.2, J1.1, J1.2, J2.2, J3.2, J6.1, J6.2, J6.3, J8.3, R2.2, R5.2, R8.2, R10.2, U1.2 (GND), U2.2 (GND), U3.8 (GND), U4.8 (GND)
unnamed: C6.2, R3.2
unnamed: C14.2, R7.2
unnamed: D2.1 (K), R4.2
unnamed: D4.1 (K), R11.2
unnamed: C8.1, C9.1, C10.1, L1.1, R1.1, R6.2, U1.3 (+)
unnamed: C15.1, C16.1, C17.1, L2.1, R9.1, R12.2, U2.3 (+)
unnamed: C24.1, U3.6 (BST)
unnamed: C7.2, R3.1, U3.4 (COMP)
unnamed: R1.2, R2.1, R4.1, U3.3 (FB)
unnamed: C24.2, L1.2, U3.9 (SW)
unnamed: C23.1, U4.6 (BST)
unnamed: C13.2, R7.1, U4.4 (COMP)
unnamed: R9.2, R10.1, R11.1, U4.3 (FB)
unnamed: C23.2, L2.2, U4.9 (SW)

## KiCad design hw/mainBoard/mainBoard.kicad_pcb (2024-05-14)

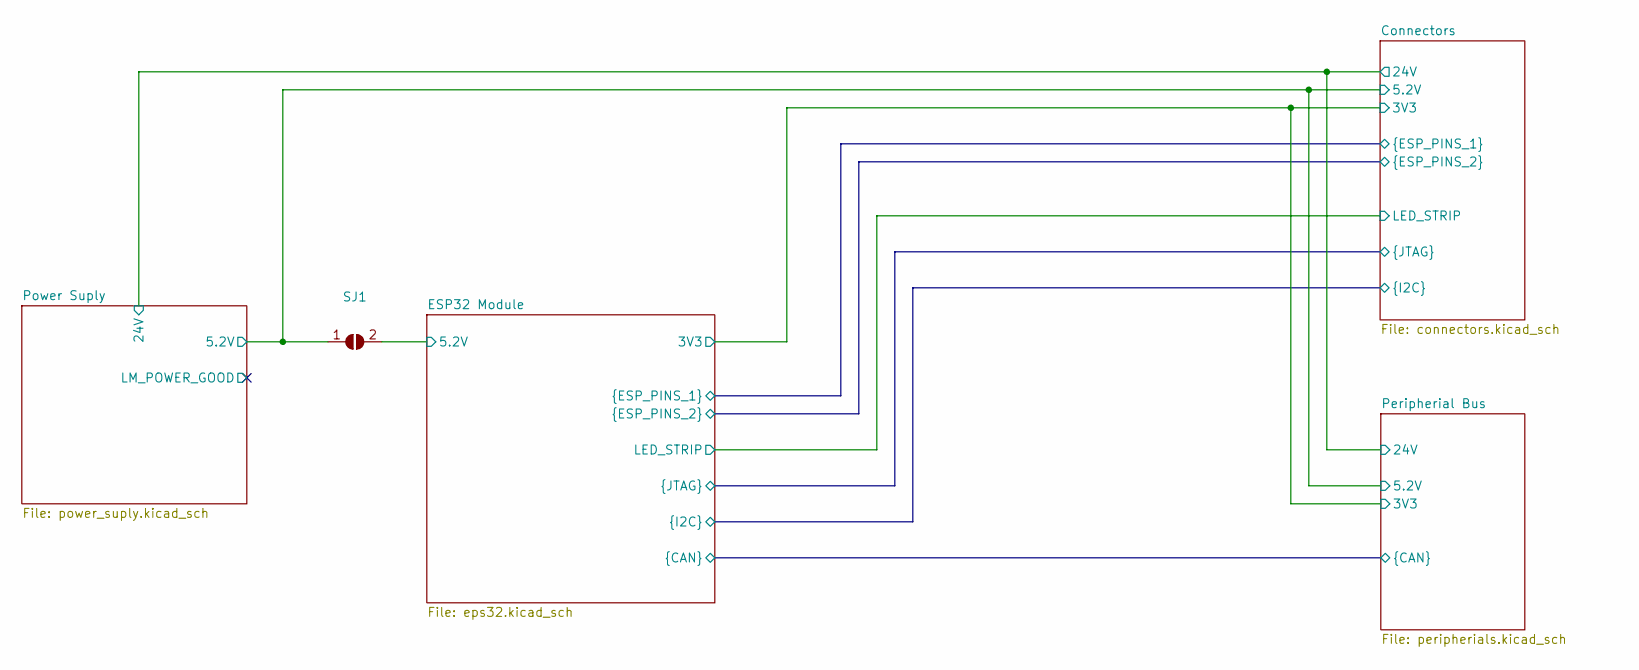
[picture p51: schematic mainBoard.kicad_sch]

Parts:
SJ1: SolderJumper_2_Open; SolderJumper-2_P1.3mm_Open_RoundedPad1.0x1.5mm

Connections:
/Connectors/5.2V: SJ1.1 (A), SJ1.2 (B); also elsewhere on the board

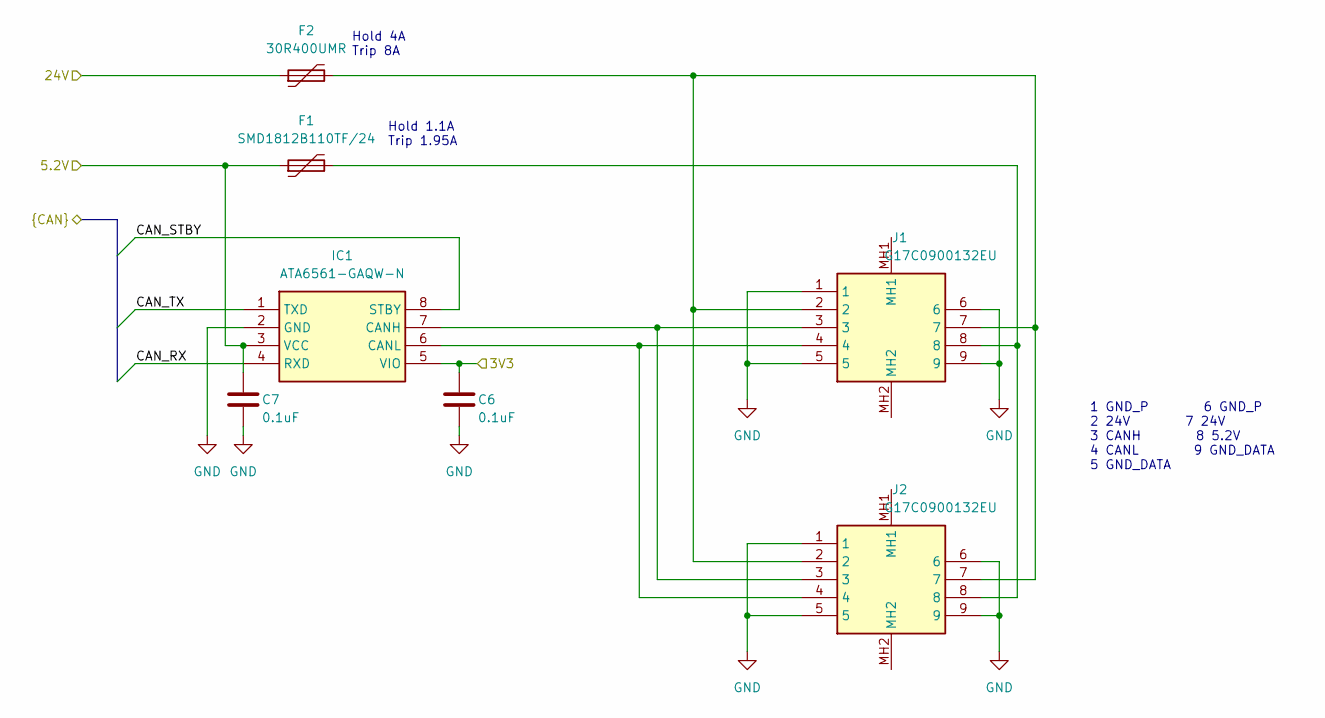
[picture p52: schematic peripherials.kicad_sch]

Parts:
C6, C7: 0.1uF; C_1206_3216Metric_Pad1.33x1.80mm_HandSolder
F1: SMD1812B110TF/24; Fuse_1812_4532Metric
F2: 30R400UMR
IC1: ATA6561-GAQW-N; SOIC127P600X175-8N; Mouser Part Number 579-ATA6561-GAQW-N
J1, J2: G17C0900132EU; Mouser Part Number 523-G17C0900132EU

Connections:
/Connectors/5.2V: C7.1, F1.1, IC1.3 (VCC); also elsewhere on the board
/Connectors/24V: F2.1; also elsewhere on the board
/Connectors/CAN_RX: IC1.4 (RXD); also elsewhere on the board
/Connectors/CAN_STBY: IC1.8 (STBY); also elsewhere on the board
/Connectors/CAN_TX: IC1.1 (TXD); also elsewhere on the board
/ESP32 Module/3V3: C6.1, IC1.5 (VIO); also elsewhere on the board
GND: C6.2, C7.2, IC1.2 (GND), J1.1, J1.5, J1.6, J1.9, J2.1, J2.5, J2.6, J2.9; also elsewhere on the board
unnamed: F2.2, J1.2, J1.7, J2.2, J2.7
unnamed: F1.2, J1.8, J2.8
unnamed: IC1.7 (CANH), J1.3, J2.3
unnamed: IC1.6 (CANL), J1.4, J2.4

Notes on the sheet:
Hold 4A Trip 8A
1 GND_P 6 GND_P 2 24V 7 24V 3 CANH 8 5.2V 4 CANL 9 GND_DATA 5 GND_DATA
Hold 1.1A Trip 1.95A

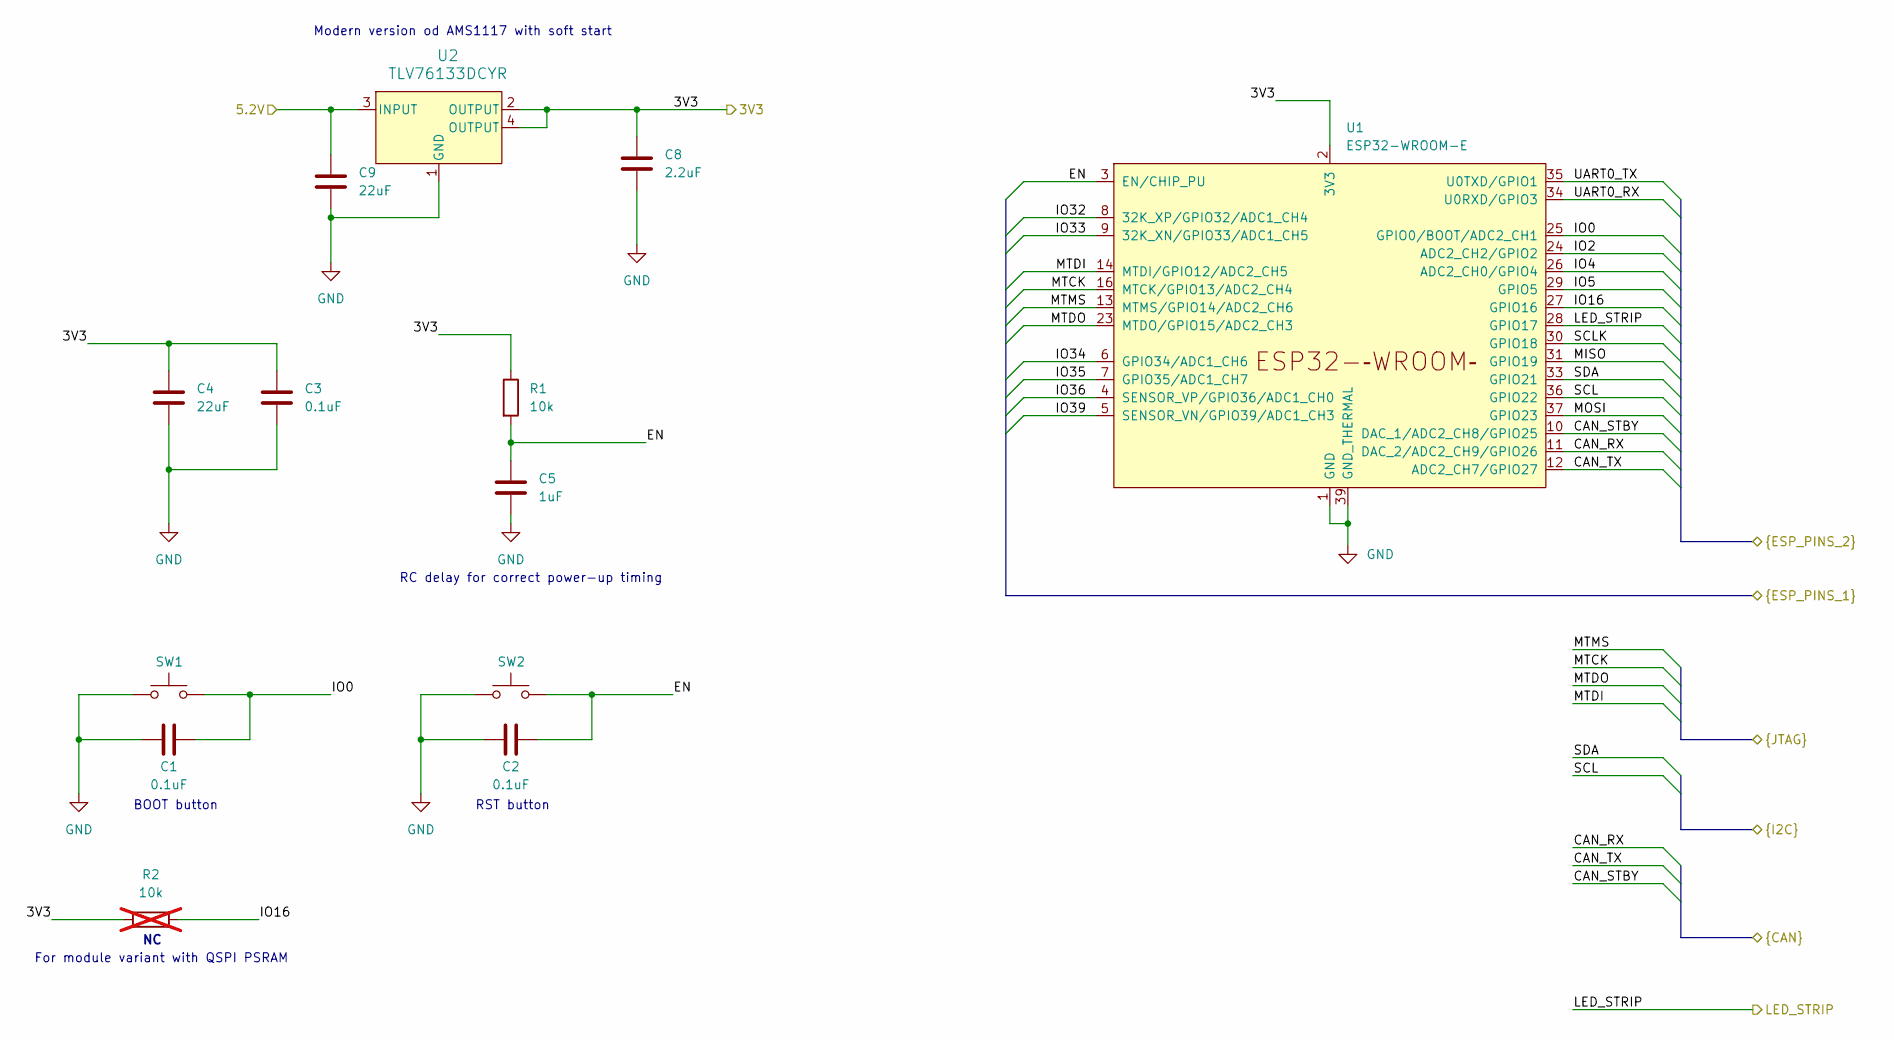
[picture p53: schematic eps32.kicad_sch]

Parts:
C1, C2, C3: 0.1uF; C_1206_3216Metric_Pad1.33x1.80mm_HandSolder
C4, C9: 22uF; C_1206_3216Metric_Pad1.33x1.80mm_HandSolder
C5: 1uF; C_1206_3216Metric_Pad1.33x1.80mm_HandSolder
C8: 2.2uF; C_1206_3216Metric_Pad1.33x1.80mm_HandSolder
R1: 10k; R_0805_2012Metric_Pad1.20x1.40mm_HandSolder
R2: 10k; R_0805_2012Metric_Pad1.20x1.40mm_HandSolder; not fitted
SW1, SW2: SW_Push; SW_SPST_B3U-1000P
U1: ESP32-WROOM-E; ESP32-WROOM-32E
U2: TLV76133DCYR; SOT_8DCYR_TEX

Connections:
/Connectors/5.2V: C9.1, U2.3 (INPUT); also elsewhere on the board
/Connectors/CAN_RX: U1.11 (DAC_2/ADC2_CH9/GPIO26); also elsewhere on the board
/Connectors/CAN_STBY: U1.10 (DAC_1/ADC2_CH8/GPIO25); also elsewhere on the board
/Connectors/CAN_TX: U1.12 (ADC2_CH7/GPIO27); also elsewhere on the board
/Connectors/EN: C2.2, C5.1, R1.2, SW2.2, U1.3 (EN/CHIP_PU); also elsewhere on the board
/Connectors/IO0: C1.2, SW1.2, U1.25 (GPIO0/BOOT/ADC2_CH1); also elsewhere on the board
/Connectors/IO2: U1.24 (ADC2_CH2/GPIO2); also elsewhere on the board
/Connectors/IO4: U1.26 (ADC2_CH0/GPIO4); also elsewhere on the board
/Connectors/IO5: U1.29 (GPIO5); also elsewhere on the board
/Connectors/IO16: R2.2, U1.27 (GPIO16); also elsewhere on the board
/Connectors/IO32: U1.8 (32K_XP/GPIO32/ADC1_CH4); also elsewhere on the board
/Connectors/IO33: U1.9 (32K_XN/GPIO33/ADC1_CH5); also elsewhere on the board
/Connectors/IO34: U1.6 (GPIO34/ADC1_CH6); also elsewhere on the board
/Connectors/IO35: U1.7 (GPIO35/ADC1_CH7); also elsewhere on the board
/Connectors/IO36: U1.4 (SENSOR_VP/GPIO36/ADC1_CH0); also elsewhere on the board
/Connectors/IO39: U1.5 (SENSOR_VN/GPIO39/ADC1_CH3); also elsewhere on the board
/Connectors/LED_STRIP: U1.28 (GPIO17); also elsewhere on the board
/Connectors/MISO: U1.31 (GPIO19); also elsewhere on the board
/Connectors/MOSI: U1.37 (GPIO23); also elsewhere on the board
/Connectors/MTCK: U1.16 (MTCK/GPIO13/ADC2_CH4); also elsewhere on the board
/Connectors/MTDI: U1.14 (MTDI/GPIO12/ADC2_CH5); also elsewhere on the board
/Connectors/MTDO: U1.23 (MTDO/GPIO15/ADC2_CH3); also elsewhere on the board
/Connectors/MTMS: U1.13 (MTMS/GPIO14/ADC2_CH6); also elsewhere on the board
/Connectors/SCL: U1.36 (GPIO22); also elsewhere on the board
/Connectors/SCLK: U1.30 (GPIO18); also elsewhere on the board
/Connectors/SDA: U1.33 (GPIO21); also elsewhere on the board
/Connectors/UART0_RX: U1.34 (U0RXD/GPIO3); also elsewhere on the board
/Connectors/UART0_TX: U1.35 (U0TXD/GPIO1); also elsewhere on the board
/ESP32 Module/3V3: C3.1, C4.1, C8.1, R1.1, R2.1, U1.2 (3V3), U2.2 (OUTPUT), U2.4 (OUTPUT); also elsewhere on the board
GND: C1.1, C2.1, C3.2, C4.2, C5.2, C8.2, C9.2, SW1.1, SW2.1, U1.1 (GND), U1.15 (GND), U1.38 (GND), U1.39 (GND_THERMAL), U2.1 (GND); also elsewhere on the board

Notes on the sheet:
RST button
BOOT button
Modern version od AMS1117 with soft start
For module variant with QSPI PSRAM
RC delay for correct power-up timing

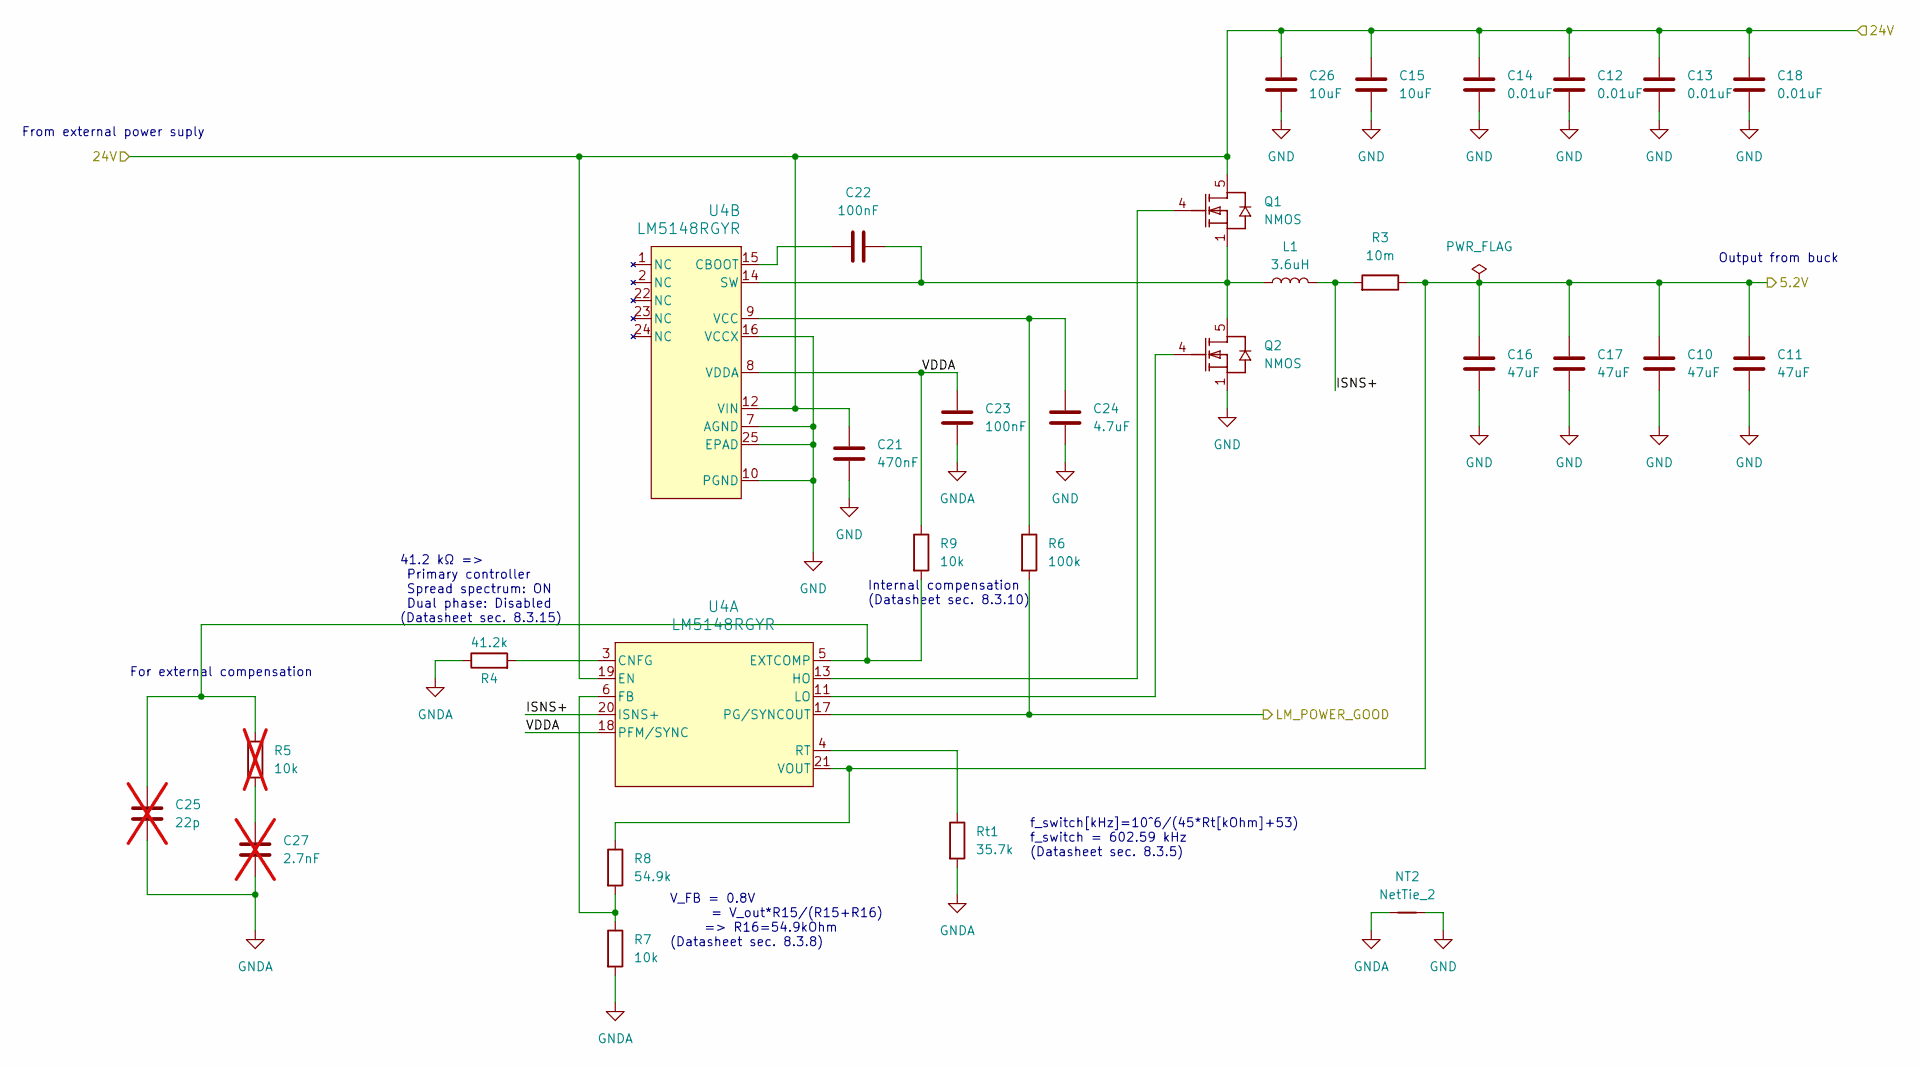
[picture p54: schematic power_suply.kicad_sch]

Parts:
C10, C11, C16, C17: 47uF; C_1210_3225Metric_Pad1.33x2.70mm_HandSolder
C12, C13, C14, C18: 0.01uF; C_0805_2012Metric_Pad1.18x1.45mm_HandSolder
C15, C26: 10uF; C_1210_3225Metric_Pad1.33x2.70mm_HandSolder
C21: 470nF; C_0805_2012Metric_Pad1.18x1.45mm_HandSolder
C22, C23: 100nF; C_0805_2012Metric_Pad1.18x1.45mm_HandSolder
C24: 4.7uF; C_0805_2012Metric_Pad1.18x1.45mm_HandSolder
C25: 22p; C_0805_2012Metric_Pad1.18x1.45mm_HandSolder; not fitted
C27: 2.7nF; C_0805_2012Metric_Pad1.18x1.45mm_HandSolder; not fitted
L1: 3.6uH; L_Bourns-SRN8040_8x8.15mm
NT2: NetTie_2; NetTie-2_SMD_Pad0.5mm
Q1, Q2: NMOS; DQJ0008A
R3: 10m; R_0815_2038Metric_Pad1.20x4.05mm_HandSolder
R4: 41.2k; R_0805_2012Metric_Pad1.20x1.40mm_HandSolder
R5: 10k; R_0805_2012Metric_Pad1.20x1.40mm_HandSolder; not fitted
R6: 100k; R_0805_2012Metric_Pad1.20x1.40mm_HandSolder
R7, R9: 10k; R_0805_2012Metric_Pad1.20x1.40mm_HandSolder
R8: 54.9k; R_0805_2012Metric_Pad1.20x1.40mm_HandSolder
Rt1: 35.7k; R_0805_2012Metric_Pad1.20x1.40mm_HandSolder
U4: LM5148RGYR; VQFN24_RGY_TEX

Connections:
/Connectors/5.2V: C10.1, C11.1, C16.1, C17.1, R3.1, R8.1, U4.21 (VOUT); also elsewhere on the board
/Connectors/24V: C12.1, C13.1, C14.1, C15.1, C18.1, C21.1, C26.1, Q1.5, Q1.6 (D), Q1.7 (D), Q1.8 (D), Q1.9, U4.12 (VIN), U4.19 (EN); also elsewhere on the board
/Power Suply/ISNS+: L1.1, R3.2, U4.20 (ISNS+)
/Power Suply/LM_POWER_GOOD: R6.2, U4.17 (PG/SYNCOUT)
/Power Suply/VDDA: C23.1, R9.1, U4.8 (VDDA), U4.18 (PFM/SYNC)
GND: C10.2, C11.2, C12.2, C13.2, C14.2, C15.2, C16.2, C17.2, C18.2, C21.2, C24.2, C26.2, NT2.2, Q2.1, Q2.2 (S), Q2.3 (S), U4.1 (NC), U4.7 (AGND), U4.10 (PGND), U4.16 (VCCX), U4.22 (NC), U4.23 (NC), U4.24 (NC), U4.25 (EPAD); also elsewhere on the board
GNDA: C23.2, C25.2, C27.2, NT2.1, R4.1, R7.2, Rt1.2; also elsewhere on the board
unnamed: C27.1, R5.2
unnamed: C25.1, R5.1, R9.2, U4.5 (EXTCOMP)
unnamed: R7.1, R8.2, U4.6 (FB)
unnamed: Q1.4, U4.13 (HO)
unnamed: Q2.4, U4.11 (LO)
unnamed: Rt1.1, U4.4 (RT)
unnamed: C22.1, U4.15 (CBOOT)
unnamed: C22.2, L1.2, Q1.1, Q1.2 (S), Q1.3 (S), Q2.5, Q2.6 (D), Q2.7 (D), Q2.8 (D), Q2.9, U4.14 (SW)
unnamed: C24.1, R6.1, U4.9 (VCC)

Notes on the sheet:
From external power suply
For external compensation
f_switch[kHz]=10^6/(45*Rt[kOhm]+53) f_switch = 602.59 kHz (Datasheet sec. 8.3.5)
Output from buck
41.2 kΩ => Primary controller Spread spectrum: ON Dual phase: Disabled (Datasheet sec. 8.3.15)
Internal compensation (Datasheet sec. 8.3.10)
V_FB = 0.8V = V_out*R15/(R15+R16) => R16=54.9kOhm (Datasheet sec. 8.3.8)

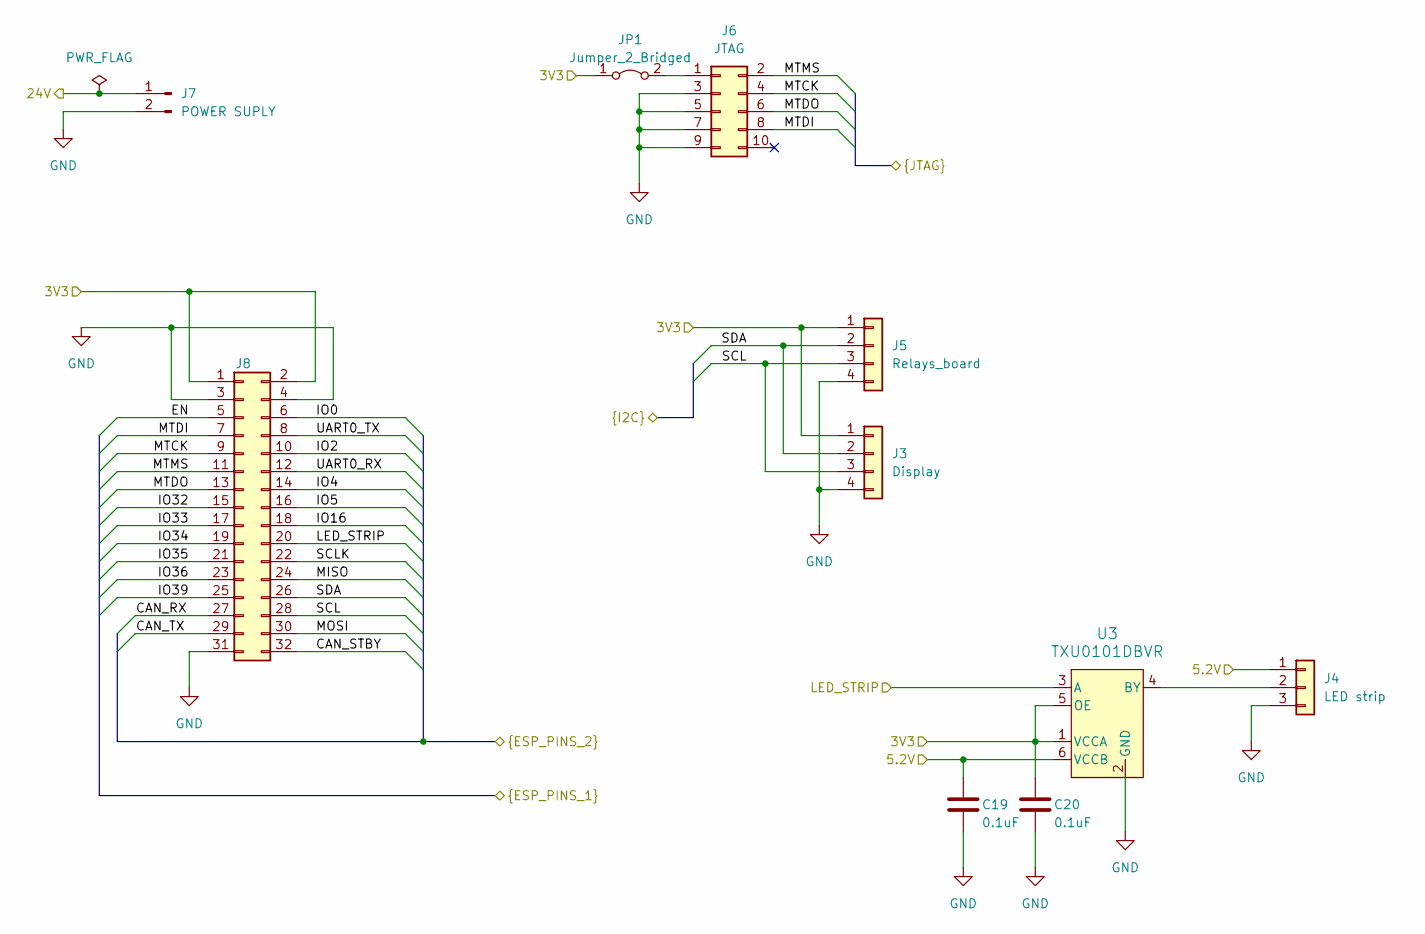
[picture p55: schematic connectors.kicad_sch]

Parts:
C19, C20: 0.1uF; C_1206_3216Metric_Pad1.33x1.80mm_HandSolder
J3: Display; JST_XH_B4B-XH-AM_1x04_P2.50mm_Vertical
J4: LED strip; JST_EH_B3B-EH-A_1x03_P2.50mm_Vertical
J5: Relays_board; JST_XH_B4B-XH-AM_1x04_P2.50mm_Vertical
J6: JTAG; PinHeader_2x05_P1.27mm_Vertical
J7: POWER SUPLY; TerminalBlock_Altech_AK300-2_P5.00mm
J8: Conn_02x16_Odd_Even; PinHeader_2x16_P2.54mm_Vertical
JP1: Jumper_2_Bridged; TestPoint_2Pads_Pitch2.54mm_Drill0.8mm
U3: TXU0101DBVR; SOT-23-6-DBV_TEX

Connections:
/Connectors/5.2V: C19.1, J4.1, U3.6 (VCCB); also elsewhere on the board
/Connectors/24V: J7.1; also elsewhere on the board
/Connectors/CAN_RX: J8.27; also elsewhere on the board
/Connectors/CAN_STBY: J8.32; also elsewhere on the board
/Connectors/CAN_TX: J8.29; also elsewhere on the board
/Connectors/EN: J8.5; also elsewhere on the board
/Connectors/IO0: J8.6; also elsewhere on the board
/Connectors/IO2: J8.10; also elsewhere on the board
/Connectors/IO4: J8.14; also elsewhere on the board
/Connectors/IO5: J8.16; also elsewhere on the board
/Connectors/IO16: J8.18; also elsewhere on the board
/Connectors/IO32: J8.15; also elsewhere on the board
/Connectors/IO33: J8.17; also elsewhere on the board
/Connectors/IO34: J8.19; also elsewhere on the board
/Connectors/IO35: J8.21; also elsewhere on the board
/Connectors/IO36: J8.23; also elsewhere on the board
/Connectors/IO39: J8.25; also elsewhere on the board
/Connectors/LED_STRIP: J8.20, U3.3 (A); also elsewhere on the board
/Connectors/MISO: J8.24; also elsewhere on the board
/Connectors/MOSI: J8.30; also elsewhere on the board
/Connectors/MTCK: J6.4, J8.9; also elsewhere on the board
/Connectors/MTDI: J6.8, J8.7; also elsewhere on the board
/Connectors/MTDO: J6.6, J8.13; also elsewhere on the board
/Connectors/MTMS: J6.2, J8.11; also elsewhere on the board
/Connectors/SCL: J3.3, J5.3, J8.28; also elsewhere on the board
/Connectors/SCLK: J8.22; also elsewhere on the board
/Connectors/SDA: J3.2, J5.2, J8.26; also elsewhere on the board
/Connectors/UART0_RX: J8.12; also elsewhere on the board
/Connectors/UART0_TX: J8.8; also elsewhere on the board
/ESP32 Module/3V3: C20.1, J3.1, J5.1, J8.1, J8.2, JP1.1 (A), U3.1 (VCCA), U3.5 (OE); also elsewhere on the board
GND: C19.2, C20.2, J3.4, J4.3, J5.4, J6.3, J6.5, J6.7, J6.9, J7.2, J8.3, J8.4, J8.31, U3.2 (GND); also elsewhere on the board
unnamed: J4.2, U3.4 (BY)
unnamed: J6.1, JP1.2 (B)

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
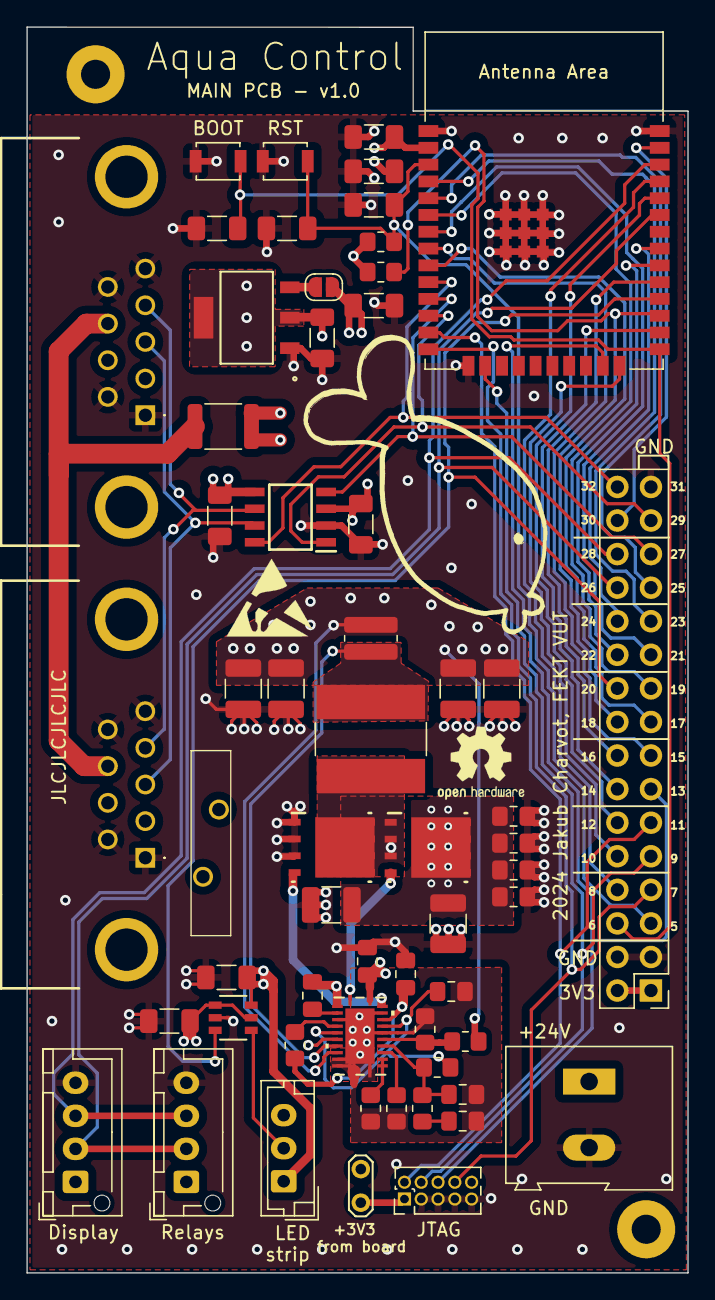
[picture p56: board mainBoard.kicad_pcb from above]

Board: 4 copper layers, 50.0 x 94.2 mm, 62 parts (0 on the bottom side), 51 nets.

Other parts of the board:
BOOT: SW_Push; SW_SPST_B3U-1000P
NT1: NetTie_2; NetTie-2_SMD_Pad0.5mm
RST: SW_Push; SW_SPST_B3U-1000P
RYBA: LOGO

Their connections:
/Connectors/EN: RST.2; also elsewhere on the board
/Connectors/IO0: BOOT.2; also elsewhere on the board
GND: BOOT.1, NT1.2, RST.1; also elsewhere on the board
GNDA: NT1.1; also elsewhere on the board

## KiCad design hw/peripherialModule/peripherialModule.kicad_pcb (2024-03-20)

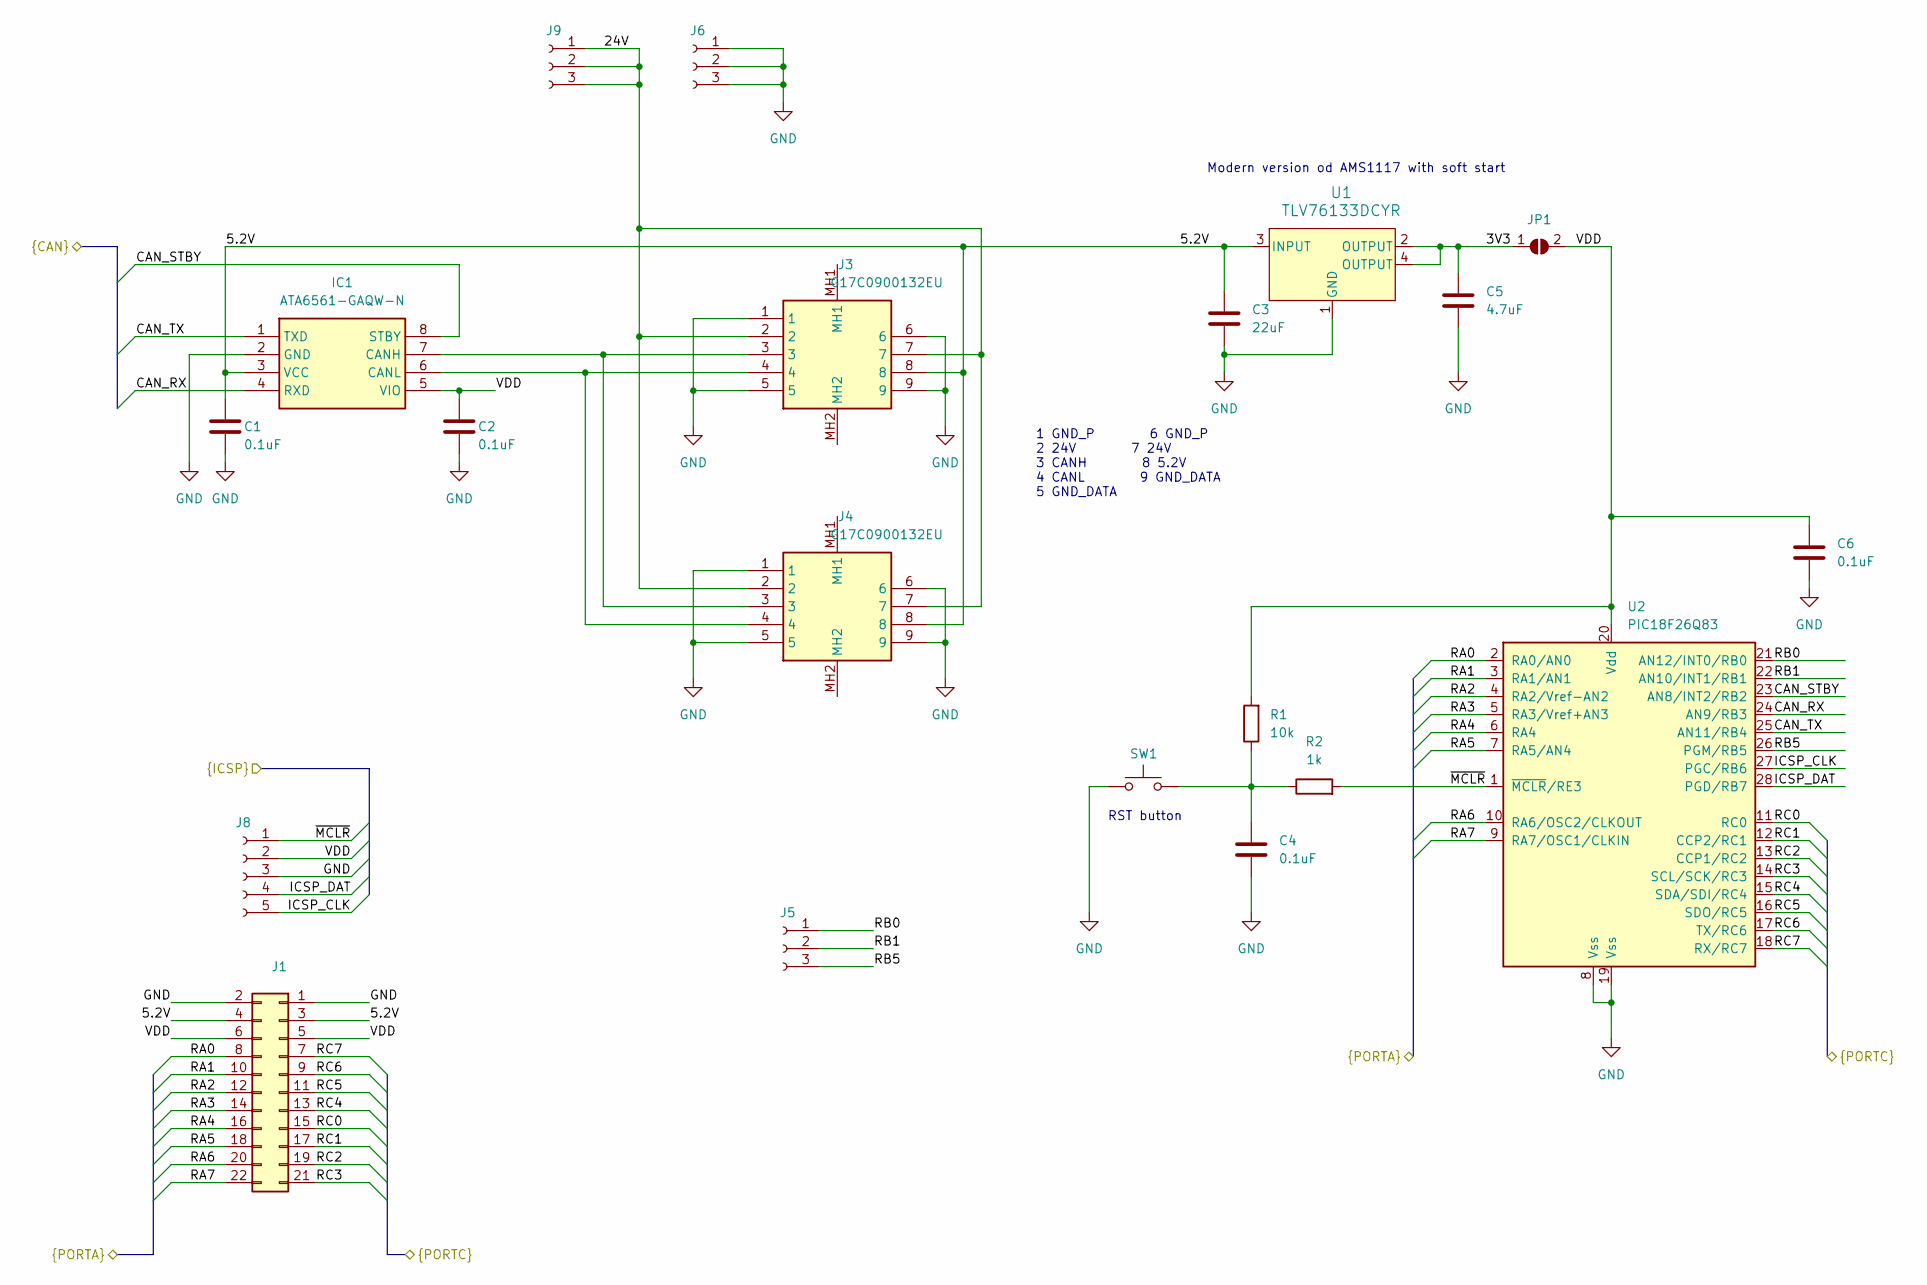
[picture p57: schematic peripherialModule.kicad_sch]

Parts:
C1, C2: 0.1uF; C_1206_3216Metric_Pad1.33x1.80mm_HandSolder
C3: 22uF; C_1206_3216Metric_Pad1.33x1.80mm_HandSolder
C4, C6: 0.1uF; C_1206_3216Metric_Pad1.33x1.80mm_HandSolder; Mouser no. 80-C1206C104K5R7210
C5: 4.7uF; C_0805_2012Metric_Pad1.18x1.45mm_HandSolder
IC1: ATA6561-GAQW-N; SOIC127P600X175-8N; Mouser Part Number 579-ATA6561-GAQW-N
J1: Conn_02x11_Socket; PinSocket_2x11_P2.54mm_Vertical
J3, J4: G17C0900132EU; Mouser Part Number 523-G17C0900132EU
J5, J6, J9: Conn_01x03_Socket; PinSocket_1x03_P2.54mm_Vertical
J8: Conn_01x05_Socket; PinSocket_1x05_P2.54mm_Vertical
JP1: SolderJumper_2_Open; SolderJumper-2_P1.3mm_Open_RoundedPad1.0x1.5mm
R1: 10k; R_0805_2012Metric_Pad1.20x1.40mm_HandSolder; Mouser no. 791-RMC20K103FTP
R2: 1k; R_0805_2012Metric_Pad1.20x1.40mm_HandSolder
SW1: SW_Push; SW_SPST_B3U-1000P
U1: TLV76133DCYR; SOT_8DCYR_TEX
U2: PIC18F26Q83; SSOP-28_5.3x10.2mm_P0.65mm

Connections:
/3V3: C5.1, JP1.1 (A), U1.2 (OUTPUT), U1.4 (OUTPUT)
/5.2V: C1.1, C3.1, IC1.3 (VCC), J1.3, J1.4, J3.8, J4.8, U1.3 (INPUT)
/24V: J3.2, J3.7, J4.2, J4.7, J9.1, J9.2, J9.3
/CAN_RX: IC1.4 (RXD), U2.24 (AN9/RB3)
/CAN_STBY: IC1.8 (STBY), U2.23 (AN8/INT2/RB2)
/CAN_TX: IC1.1 (TXD), U2.25 (AN11/RB4)
/ICSP_CLK: J8.5, U2.27 (PGC/RB6)
/ICSP_DAT: J8.4, U2.28 (PGD/RB7)
/RA0: J1.8, U2.2 (RA0/AN0)
/RA1: J1.10, U2.3 (RA1/AN1)
/RA2: J1.12, U2.4 (RA2/Vref-AN2)
/RA3: J1.14, U2.5 (RA3/Vref+AN3)
/RA4: J1.16, U2.6 (RA4)
/RA5: J1.18, U2.7 (RA5/AN4)
/RA6: J1.20, U2.10 (RA6/OSC2/CLKOUT)
/RA7: J1.22, U2.9 (RA7/OSC1/CLKIN)
/RB0: J5.1, U2.21 (AN12/INT0/RB0)
/RB1: J5.2, U2.22 (AN10/INT1/RB1)
/RB5: J5.3, U2.26 (PGM/RB5)
/RC0: J1.15, U2.11 (RC0)
/RC1: J1.17, U2.12 (CCP2/RC1)
/RC2: J1.19, U2.13 (CCP1/RC2)
/RC3: J1.21, U2.14 (SCL/SCK/RC3)
/RC4: J1.13, U2.15 (SDA/SDI/RC4)
/RC5: J1.11, U2.16 (SDO/RC5)
/RC6: J1.9, U2.17 (TX/RC6)
/RC7: J1.7, U2.18 (RX/RC7)
/VDD: C2.1, C6.1, IC1.5 (VIO), J1.5, J1.6, J8.2, JP1.2 (B), R1.2, U2.20 (Vdd)
/~MCLR: J8.1, R2.2, U2.1 (~MCLR/RE3)
GND: C1.2, C2.2, C3.2, C4.2, C5.2, C6.2, IC1.2 (GND), J1.1, J1.2, J3.1, J3.5, J3.6, J3.9, J4.1, J4.5, J4.6, J4.9, J6.1, J6.2, J6.3, J8.3, SW1.1, U1.1 (GND), U2.8 (Vss), U2.19 (Vss)
unnamed: C4.1, R1.1, R2.1, SW1.2
unnamed: IC1.7 (CANH), J3.3, J4.3
unnamed: IC1.6 (CANL), J3.4, J4.4

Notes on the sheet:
1 GND_P 6 GND_P 2 24V 7 24V 3 CANH 8 5.2V 4 CANL 9 GND_DATA 5 GND_DATA
RST button
Modern version od AMS1117 with soft start

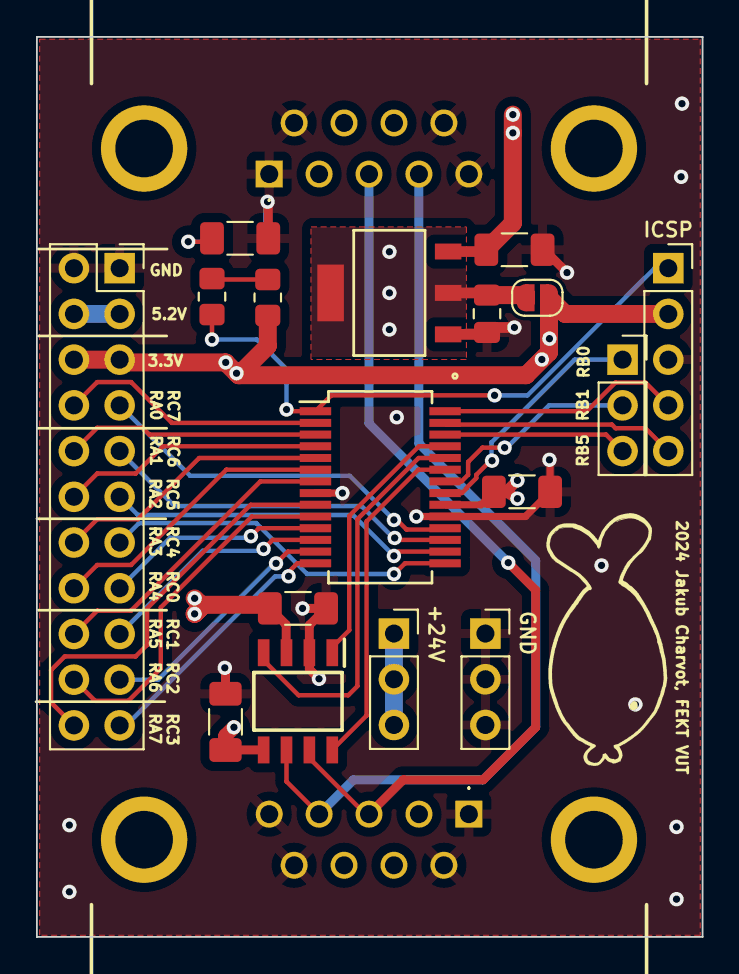
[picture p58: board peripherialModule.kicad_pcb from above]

Board: 4 copper layers, 37.0 x 50.0 mm, 20 parts (1 on the bottom side), 33 nets.

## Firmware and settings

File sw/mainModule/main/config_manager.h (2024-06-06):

#ifndef CONFIG_MANAGER_H
#define CONFIG_MANAGER_H

#include "driver/gpio.h"
#include "esp_log.h"

#include <stdio.h>
#include <stdlib.h>
#include <inttypes.h>
#include "freertos/FreeRTOS.h"
#include "freertos/task.h"
#include "freertos/semphr.h"
#include "esp_err.h"
#include "cJSON.h"
#include "nvs_flash.h"
#include "nvs.h"

#include "pins.h"
#include "status_control.h"
#include "wifi_driver.h"

#define NVS_NAMESPACE_MODULE_CONFIG "modulecfg"
#define NVS_NAMESPACE_SYSTEM_CONFIG "syscfg"

extern SemaphoreHandle_t config_control_sem;
extern uint64_t CONFIG_VERSION_from_web;


typedef struct 
{
    bool    manual;
    uint8_t timer_on_hours;
    uint8_t timer_on_minutes;
    uint8_t timer_off_hours;
    uint8_t timer_off_minutes;
    bool    manual_state;
} config_relay_t;

typedef struct
{
    bool active;
    float max_value;
    float min_value;
} config_alarm_t;

#define DEFAULT_CONFIG_ALARM (config_alarm_t){false,0.0,0.0}

// SYSTEM config
//--------------------
// not all the attributes from json
typedef struct 
{
    config_relay_t* relays; 
} config_system_t;



// modules config
//--------------------
// NODE_TYPE_LED_BOARD
typedef struct
{
    uint8_t start_time_hours;
    uint8_t start_time_minutes;
    uint8_t end_time_hours;
    uint8_t end_time_minutes;
    uint8_t fall_time; // duration in minutes
    uint8_t rise_time; // duration in minutes
    uint8_t intensity;
} config_ledstrip_t;

#define DEFAULT_CONFIG_LEDSTRIP (config_ledstrip_t){0,0,0,0,0,0,0}

typedef struct
{
    config_ledstrip_t ledstrip_0;
    config_ledstrip_t ledstrip_1;
} config_module_led_board_t;

#define DEFAULT_CONFIG_MODULE_LED_BOARD (config_module_led_board_t){DEFAULT_CONFIG_LEDSTRIP,DEFAULT_CONFIG_LEDSTRIP}

// NODE_TYPE_TEMP_SENSOR
typedef struct
{
    config_alarm_t alarm_cfg;
} config_module_temp_sens_t;

#define DEFAULT_CONFIG_MODULE_TEMP_SENS (config_module_temp_sens_t){DEFAULT_CONFIG_ALARM}

// NODE_TYPE_WATER_LEVEL_SENSOR
typedef struct
{
    config_alarm_t alarm_cfg;
} config_module_wl_sens_t;

#define DEFAULT_CONFIG_MODULE_WL_SENS   (config_module_wl_sens_t){DEFAULT_CONFIG_ALARM}

// NODE_TYPE_PH_SENSOR
typedef struct
{
    config_alarm_t alarm_cfg;
} config_module_ph_sens_t;

#define DEFAULT_CONFIG_MODULE_PH_SENS   (config_module_ph_sens_t){DEFAULT_CONFIG_ALARM}

esp_err_t config_manager_init();

bool config_is_obsolete();

esp_err_t config_update_from_web();
esp_err_t config_module_load_from_nvm(node_sn_t node_sn, node_type_t node_type, void* module_cfg);
esp_err_t config_load_nvm_all(config_system_t* system_config, can_node_t* can_connected_nodes, uint8_t can_num_address_given);




#endif /* CONFIG_MANAGER_H*/

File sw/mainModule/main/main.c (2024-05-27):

/* 
   TODO: License or other funny thing
*/




#include "driver/gpio.h"
#include "esp_log.h"

#include <stdio.h>
#include <stdlib.h>
#include <inttypes.h>
#include "freertos/FreeRTOS.h"
#include "freertos/task.h"
#include "freertos/semphr.h"
#include "esp_err.h"

#include "globals.h"
#include "pins.h"
#include "debug_functions.h"
#include "status_leds_driver.h"
#include "status_control.h"
#include "CAN_driver.h"
#include "temp_sensor_driver.h"
#include "water_level_sensor_driver.h"
#include "relays_driver.h"
#include "wifi_driver.h"
#include "config_manager.h"
#include "control_routines.h"
#include "time_driver.h"




#define STATS_TASK_PRIO     3
#define STATS_TICKS         pdMS_TO_TICKS(1000)


static SemaphoreHandle_t sync_control_task;
static SemaphoreHandle_t sync_status_update_task;
static SemaphoreHandle_t sync_status_task_init_done;
static SemaphoreHandle_t sync_fw_OTA_task;
static SemaphoreHandle_t sync_wifi_task;
static SemaphoreHandle_t sync_can_bus_task;
static SemaphoreHandle_t sync_stats_task;
static SemaphoreHandle_t sync_display_task;

static const char *TAG = "mainBoard - main.c";








static void control_task(void *arg)
{
    xSemaphoreTake(sync_control_task, portMAX_DELAY);
    ESP_LOGI(TAG,"Entering task: control_task");

    ESP_LOGI(TAG,"control_task -- starting others");
    xSemaphoreGive(sync_status_update_task);
    // Wait for status control init
    ESP_LOGI(TAG,"control_task -- waiting for init done");
    xSemaphoreTake(sync_status_task_init_done, portMAX_DELAY);
    // Define this module status
    set_control_module_status(MODST_STARTUP);
    // Init services without own task
    relays_init();
    config_manager_init();
    set_timezone("CET-1CEST,M3.5.0/2,M10.5.0/3");
    
    // Start other tasks 
    xSemaphoreGive(sync_wifi_task);
    xSemaphoreGive(sync_fw_OTA_task);
    xSemaphoreGive(sync_can_bus_task);
    xSemaphoreGive(sync_display_task);

    ESP_LOGI(TAG,"Control task -- preparing CAN modules");
    if(ESP_OK != control_prepare_can_modules(pdMS_TO_TICKS(10000)))
    {
        ESP_LOGE(TAG,"control_prepare_can_modules failed ...");
        set_control_module_status(MODST_ERROR);
    }
    else
    {
        set_control_module_status(MODST_READY);
    }


    while (1) {
        // routine is internally checks period of each operation
        printf("Entering control routine \n");
        control_routine();
    }
}



static void status_update_task(void *arg)
{
    xSemaphoreTake(sync_status_update_task, portMAX_DELAY);
    ESP_LOGI(TAG,"Entering task: status_update_task");

    ESP_ERROR_CHECK(status_control_init());
    // Notify about init done - unblock other tasks
    xSemaphoreGive(sync_status_task_init_done);
    ESP_ERROR_CHECK(status_leds_init());
    vTaskDelay(100 / portTICK_PERIOD_MS);
    ESP_LOGI(TAG,"Status update task - %d \n", STATUS_device);

    while (1) {
        // TODO
        device_status_t old_status = STATUS_device;
        process_device_status();
        if(old_status != STATUS_device)
        {
            printf("Device status changed to %d\n", STATUS_device);
        }
        status_leds_update(STATUS_device);
        vTaskDelay(500 / portTICK_PERIOD_MS);
        // status_leds_update(STATUS_device);
    }
}

static void fw_OTA_task(void *arg)
{
    xSemaphoreTake(sync_fw_OTA_task, portMAX_DELAY);
    ESP_LOGI(TAG,"Entering task: fw_OTA_task");
    // initialization
    set_ota_module_status(MODST_READY);

    while (1) {
        // TODO
        vTaskDelay(1000 / portTICK_PERIOD_MS);
    }
}

static void wifi_task(void *arg)
{
    xSemaphoreTake(sync_wifi_task, portMAX_DELAY);
    ESP_LOGI(TAG,"Entering task: wifi_task");

    // Initialize Wi-Fi
    wifi_init_sta();


    while (1) {
        wifi_driver_routine();
    }
}

static void can_bus_task(void *arg)
{
    xSemaphoreTake(sync_can_bus_task, portMAX_DELAY);
    ESP_LOGI(TAG,"Entering task: can_bus_task");
    // initialization
    set_can_module_status(MODST_STARTUP);
    ESP_ERROR_CHECK(can_driver_init());
    set_can_module_status(MODST_READY);

    while (1) 
    {
        // Procces rx each 300 ms or on demand
        xSemaphoreTake(can_rx_sem,300/portTICK_PERIOD_MS);
        can_proccess_rx();
    }

    ESP_ERROR_CHECK(can_driver_deinit());
    vTaskDelete(NULL);
}

static void display_task(void *arg)
{
    xSemaphoreTake(sync_display_task, portMAX_DELAY);
    ESP_LOGI(TAG,"Entering task: display_task");
    // initialization
    set_display_module_status(MODST_READY);

    while (1) {
        // TODO
        vTaskDelay(1000 / portTICK_PERIOD_MS);
    }
}


static void stats_task(void *arg)
{
    xSemaphoreTake(sync_stats_task, portMAX_DELAY);
    ESP_LOGI(TAG,"Entering task: stats_task");

    //Print real time stats periodically
    while (1) {
        printf("\n\nGetting real time stats over %"PRIu32" ticks\n", STATS_TICKS);
        esp_err_t statusCode = print_real_time_stats(STATS_TICKS); 
        if (statusCode == ESP_OK) {
            printf("Real time stats obtained\n");
        } 
        else if (statusCode == ESP_ERR_INVALID_SIZE){
            printf("Invalid size :(\n");
        }
        
        else {
            printf("Error getting real time stats: %d\n",statusCode);
        }
        vTaskDelay(pdMS_TO_TICKS(1000));
    }
}




void app_main(void)
{
    //Allow other core to finish initialization
    vTaskDelay(pdMS_TO_TICKS(100));
    
    // Initialize NVS (Flash)
    esp_err_t ret = nvs_flash_init();
    if (ret == ESP_ERR_NVS_NO_FREE_PAGES || ret == ESP_ERR_NVS_NEW_VERSION_FOUND) {
      ESP_ERROR_CHECK(nvs_flash_erase());
      ret = nvs_flash_init();
    }
    ESP_ERROR_CHECK(ret);

    //Create semaphores to synchronize
    sync_stats_task = xSemaphoreCreateBinary();
    sync_status_update_task = xSemaphoreCreateBinary();
    sync_wifi_task = xSemaphoreCreateBinary();
    sync_fw_OTA_task = xSemaphoreCreateBinary();
    sync_can_bus_task = xSemaphoreCreateBinary();
    sync_display_task = xSemaphoreCreateBinary();
    sync_control_task = xSemaphoreCreateBinary();
    sync_status_task_init_done = xSemaphoreCreateBinary();


    // TODO: update priorities
    //Create stats task
    xTaskCreatePinnedToCore(stats_task, "stats", 4096, NULL, STATS_TASK_PRIO, NULL, 0);
    //Create status task
    xTaskCreatePinnedToCore(status_update_task, "status update", 4096, NULL, 4, NULL, 1);
    //Create wifi task
    xTaskCreatePinnedToCore(wifi_task, "wifi", 4096, NULL, STATS_TASK_PRIO, NULL, 0);
    //Create OTA task
    xTaskCreatePinnedToCore(fw_OTA_task, "fw_OTA_task", 4096, NULL, STATS_TASK_PRIO, NULL, 0);
    //Create CAN task
    xTaskCreatePinnedToCore(can_bus_task, "can_bus_task", 4096, NULL, STATS_TASK_PRIO, NULL, 0);
    //Create status task
    xTaskCreatePinnedToCore(display_task, "display_task", 4096, NULL, STATS_TASK_PRIO, NULL, 0);
    //Create control task
    xTaskCreatePinnedToCore(control_task, "control_task", 4096, NULL, STATS_TASK_PRIO, NULL, 0);

    
    //Start control task
    xSemaphoreGive(sync_control_task);
    // xSemaphoreGive(sync_stats_task);

    // debug 





    while (1)
    {
        vTaskDelay(10000 / portTICK_PERIOD_MS);
    }

}

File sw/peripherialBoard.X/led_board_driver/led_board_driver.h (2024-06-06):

/* Microchip Technology Inc. and its subsidiaries.  You may use this software 
 * and any derivatives exclusively with Microchip products. 
 * 
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
 * IN NO EVENT WILL MICROCHIP BE LIABLE FOR ANY INDIRECT, SPECIAL, PUNITIVE, 
 * INCIDENTAL OR CONSEQUENTIAL LOSS, DAMAGE, COST OR EXPENSE OF ANY KIND 
 * WHATSOEVER RELATED TO THE SOFTWARE, HOWEVER CAUSED, EVEN IF MICROCHIP HAS 
 * BEEN ADVISED OF THE POSSIBILITY OR THE DAMAGES ARE FORESEEABLE.  TO THE 
 * FULLEST EXTENT ALLOWED BY LAW, MICROCHIP'S TOTAL LIABILITY ON ALL CLAIMS 
 * IN ANY WAY RELATED TO THIS SOFTWARE WILL NOT EXCEED THE AMOUNT OF FEES, IF 
 * ANY, THAT YOU HAVE PAID DIRECTLY TO MICROCHIP FOR THIS SOFTWARE.
 *
 * MICROCHIP PROVIDES THIS SOFTWARE CONDITIONALLY UPON YOUR ACCEPTANCE OF THESE 
 * TERMS. 
 */

/* 
 * File:   
 * Author: 
 * Comments:
 * Revision history: 
 */

// This is a guard condition so that contents of this file are not included
// more than once.  
#ifndef LED_BOARD_DRIVER_H
#define	LED_BOARD_DRIVER_H

#include "../mcc_generated_files/system/system.h"
#include <stdint.h>

#if DEVICE_TYPE == DEVICE_TYPE_LED_BOARD

// PR register = 355 (0x163)
#define LED_PWM_MIN 100
#define LED_PWM_MAX 355

typedef enum
{
    LED_CH_0 = 0,
    LED_CH_1 = 1,        
} led_channel_t;

void led_enable_channel(led_channel_t channel);
void led_disable_channel(led_channel_t channel);
void led_set_brightness(led_channel_t channel, uint8_t brightness);

void led_board_init(void);

void led_board_can_ch0_set_brightness(uint8_t brightness);
void led_board_can_ch1_set_brightness(uint8_t brightness);

node_status_t led_board_routine(void);





#ifdef	__cplusplus
extern "C" {
#endif /* __cplusplus */

    // TODO If C++ is being used, regular C code needs function names to have C 
    // linkage so the functions can be used by the c code. 

#ifdef	__cplusplus
}
#endif /* __cplusplus */

#endif /* DEVICE_TYPE == DEVICE_TYPE_LED_BOARD */

#endif	/* LED_BOARD_DRIVER_H */

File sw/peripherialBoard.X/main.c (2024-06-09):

/*
 * File:   main.c
 * Author: jakub
 *
 * Created on April 13, 2024, 10:21 AM
 */


// Do not forgot to specify device type in device_type.h !!

#include "mcc_generated_files/system/system.h"
#include "device_type.h"
#include "can_driver/can_driver.h"
#include "../shared/CAN_definitions.h"
#include "temp_sensor_driver/temp_sensor_driver.h"
#include "water_level_driver/water_level_driver.h"



uint8_t led_brightness = 0;





void timer0ISR(void)
{
    counter_second++;
    
    if(counter_second >= 2)
    {
//        LED_PIN_Toggle();
//        UART1_println("ping\0");
//        CAN_SendDebugPrint("debug\0");
    }
//    LED1_FB_Toggle();
//    LED0_FB_Toggle();
//    led_brightness += 20;
//    led_set_brightness(LED_CH_0,led_brightness);
//    
}






void main(void) 
{
    SYSTEM_Initialize();
    TMR0_OverflowCallbackRegister(timer0ISR);
    INTCON0bits.GIE = 1;
    CAN_SendDebugPrint("System started");
    
    while(counter_second < 3)
    {
        
    }

    


    
    
            
    // If using interrupts in PIC18 High/Low Priority Mode you need to enable the Global High and Low Interrupts 
    // If using interrupts in PIC Mid-Range Compatibility Mode you need to enable the Global Interrupts 
    // Use the following macros to: 

    // Enable the Global Interrupts 
//    INTERRUPT_GalobalInterruptEnable(); 
//    LED_PIN_Toggle();
    
    #if DEVICE_TYPE == DEVICE_TYPE_LED_BOARD
        led_board_init();
    #endif
    

    
    
    while(1)
    {
        #if DEVICE_TYPE == DEVICE_TYPE_LED_BOARD
            GLOBAL_device_status = led_board_routine();
            __delay_ms(200); // for accurate intensity switch
        #elif DEVICE_TYPE == DEVICE_TYPE_TEMP_SENSOR
            GLOBAL_device_status = temp_sensor_routine();
            __delay_ms(1000);
        #elif DEVICE_TYPE == DEVICE_TYPE_WATER_LEVEL_SENSOR
            GLOBAL_device_status = water_level_routine();
            __delay_ms(200);
        #else
            #error "Not supported DEVICE_TYPE"
        #endif
        
    }    
    return;
}

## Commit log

2023-11-12 hw - schema work in progress
    [ESP32 Pins (copy 2).xlsx, connectors.kicad_sch, eps32.kicad_sch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]
2023-11-17 hw - kicad neco
    [eps32.kicad_sch, peripherials.kicad_sch]
2023-12-03 hw + blok schema
    [DBV0006A.stp, ESP32 Pins (copy 2).xlsx, connectors.kicad_sch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]
2023-12-05 nejaky hw + teorie + desky
    [connectors.kicad_sch, eps32.kicad_sch, mainBoard.kicad_sch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]
2023-12-08 hw - changed uart2 pins, latex- ridici jednotka
    [ESP32 Pins (copy 2).xlsx, connectors.kicad_sch, eps32.kicad_sch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]
2023-12-11 text - napajeci obvod, ochrany, 230v + pomocne schema v kicadu
    [power_suply.kicad_sch, ukazky-do-textu.kicad_pcb, ukazky-do-textu.kicad_sch]
2023-12-11 hw - rezistory
    [peripherials.kicad_sch]
2023-12-17 struktura a cleanup
    [ESP32 Pins.xlsx]
2024-02-06 drawing layout
    [30R400UMR.PcbLib, 30R400UMR.SchLib, 30R400UMR.stp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]
2024-02-06 more steps to the finale
    [mainBoard.kicad_pcb]
2024-02-10 lot of hw
    [eps32.kicad_sch, mainBoard.kicad_pcb]
2024-02-10 buck vedle
    [mainBoard.kicad_pcb, power_suply.kicad_sch]
2024-02-11 hotovo bez silkscreenu
    [mainBoard.kicad_pcb]
2024-02-11 finale bez rybicky
    [EDI2CAP.CFG, SRN8040-101M.SLDPRT, SRN8040-101M.stp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]
2024-02-11 gerbere s rybou
    [mainBoard-B_Cu.gbl, mainBoard-B_Mask.gbs, mainBoard-B_Paste.gbp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]
2024-02-14 gerber zip
2024-02-19 moc toho
    [726386-2.psm, 726386-2.stp, EDI2CAP.CFG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]
2024-03-06 boards are changing
    [FB_devider.xlsx, connectors.kicad_sch, ledBoard.kicad_pcb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]
2024-03-20 hw - ledBoard
    [726386-2.psm, EDI2CAP.CFG, L7986A.stp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]
2024-03-20 hw - ledboard, compensation
    [FB_devider.xlsx, ledBoard.kicad_pcb, ledBoard.kicad_sch]
2024-03-31 hw - led board redesign
    [EDI2CAP.CFG, ETQP4M100KFN.stp, FB_devider.xlsx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]
2024-05-02 hw - bom
2024-05-02 notes and thouths
    [CAN_Adresses.xlsx]
2024-05-02 sw - tasks, led strip
2024-05-08 sw - peripherial init and mainBoard status leds
    [CAN_Adresses.xlsx]
2024-05-11 sw - temp sensor master + slave, general things
    [CAN_Adresses.xlsx, PIC_pin_allocation.xlsx]
2024-05-12 FW 0.1 - temp sensor
    [CAN_Adresses.xlsx]
2024-05-14 sw - water level rozpracovano
    [CAN_Adresses.xlsx, PIC_pin_allocation.xlsx]
2024-05-14 text - dps hlavni jednotky, not final
    [mainBoard.kicad_pcb]
2024-05-14 text - periferie, obrazky hw - schemata
    [eps32.kicad_sch, ledBoard.kicad_sch, peripherialModule.kicad_sch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]
2024-05-15 schemata a 3d modely pro text
    [ledBoard.kicad_pcb, ukazky-do-textu.kicad_sch]
2024-05-15 text-modul periferie + led board
2024-05-16 text - revize napsaneho, schema lm
    [main-b-simply.kicad_sch, ukazky-do-textu.kicad_sch]
2024-05-19 sw - mainBoard wifi and i2c relays
2024-05-22 sw - bugfix can mutex release
    [CAN_driver.c]
2024-05-24 sw - perif, pins corrected
    [pins.h]
2024-05-24 text - 230v, wl sensor
    [relays.kicad_sch, ukazky-do-textu.kicad_sch]
2024-05-27 correct payload info
    [CAN_Adresses.xlsx]
2024-05-27 sw - control routine forst half + many bugfixes
    [CAN_driver.c, common_types.h, config_manager.h]
2024-05-28 oprava schematicu
    [power_suply.kicad_sch]
2024-06-06 sw - some rework
    [CAN_definitions.h, config_manager.h, led_board_driver.c]
2024-06-09 memory leak + led improve
    [CAN_driver.c, led_board_driver.c, led_board_driver.h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]
